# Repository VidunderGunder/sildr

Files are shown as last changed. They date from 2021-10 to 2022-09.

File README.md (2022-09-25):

# Sildr

Everything Sildr and technical.

1.0 and 2.0 are legacy, and some relevant documentation can be found in `/legacy`. Keep in mind it's mostly in Norwegian.

## Order History

**Components:**  
https://no.mouser.com/OrderHistory/OrdersView.aspx  
Email: kristiankramas@outlook.com  
Username: `vidundergunder`  
Password: `******`

**PCB:**  
https://jlcpcb.com/order#EL  
Email: kristiankramas@outlook.com  
Username: `vidundergunder`  
Password: `******`

## Electrical System v3.0

### Overview Illustration (click on image to open Figma):

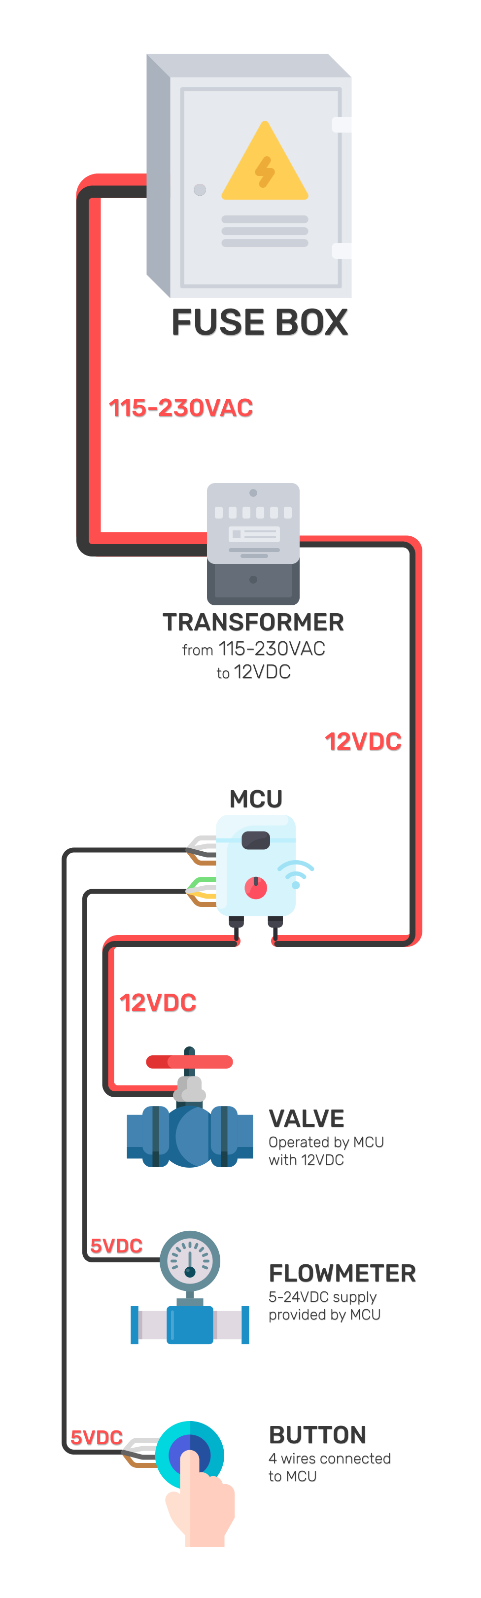
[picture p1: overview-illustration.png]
overview-illustration (https://www.figma.com/file/0GwcSEPVadjQJGAlymwUbZ/Sildr-Electronics?node-id=0%3A1)


The system is split in two parts:

1. Base system
2. Optional data logging system (requires the base system)

### Base System

#### Simplified circuit diagram (click on image to run simulation):

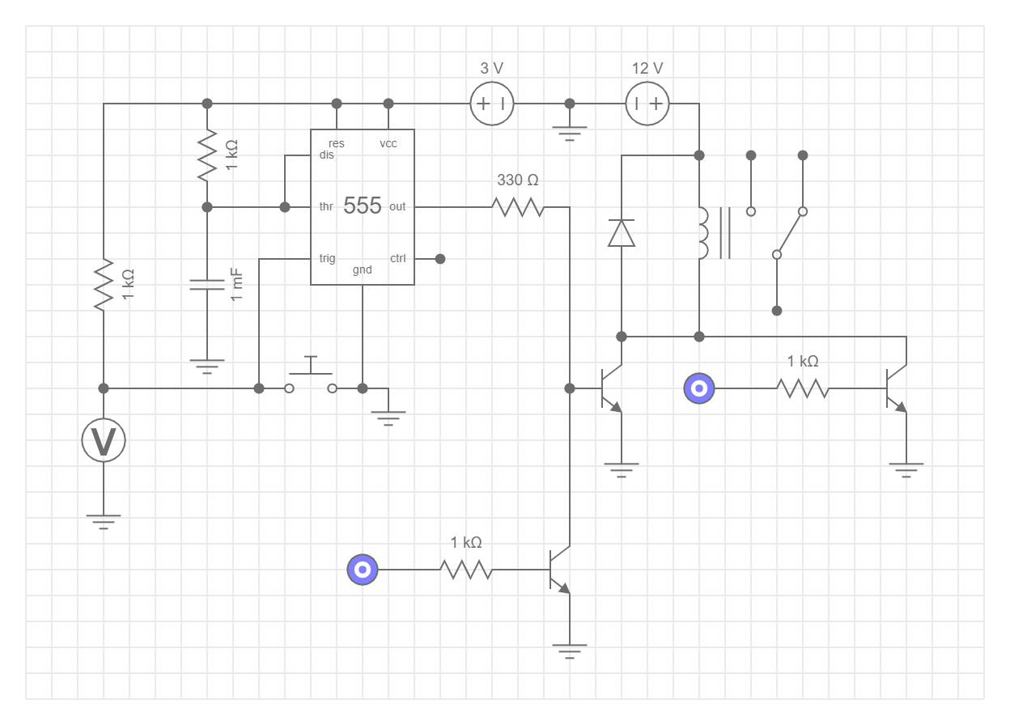
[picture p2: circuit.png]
circuit (https://everycircuit.com/circuit/6050376572469248/sildr-v3.0-base)


> _Image may be outdated_
> 
> - Behavior can be controlled with an MCU, and has an analog fallback
> - Relay represents the solenoid valve
> - Voltmeter is a digital in pin, registering 0V as button presses
> - Logic sources are digital out pins
> - Resistor connected to pin 7 and 6 on the 555-timer can be changed out for a potentiometer to manually set timer on-site

#### Simulated Prototype Circuit (click on image to run simulation):

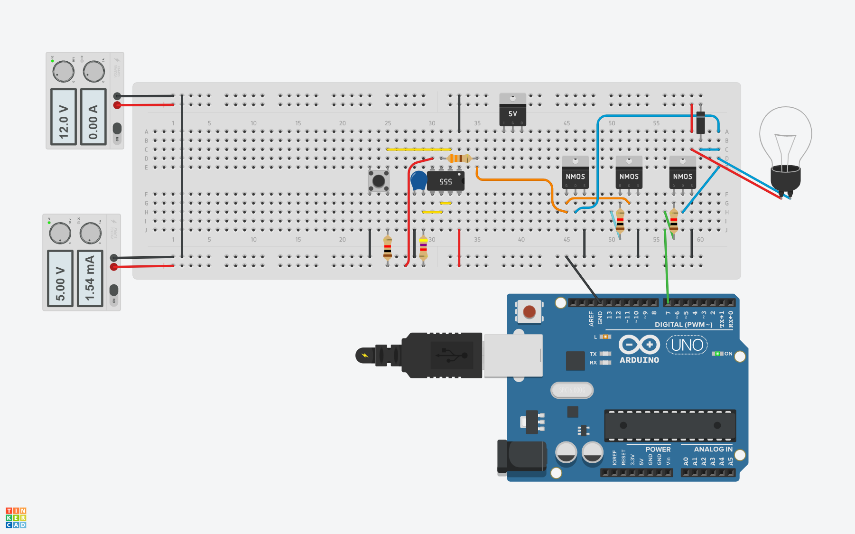
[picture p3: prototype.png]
prototype (https://www.tinkercad.com/things/aFhGxdh2pm7-epic-kieran-snaget/editel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)


> _Image may be outdated_  
> 
> - Simulation requires an Autodesk account (you can use your google account)
> - Lightbulb represents the solenoid valve

#### Prototype Components

- 1x 555-timer
- 3x nMOS Transistor (MOSFET)  
(FQP30N06L 60V LOGIC N-Channel MOSFET)
- 3x 1k resistor
- 1x 4k7 resistor
- 1x 330 resistor
- 1x 1mF capacitor
- 1x Pushbutton
- 1x diode
- 12V DC power supply
- 5V DC power supply

#### Production Components

| Component | Description | Image |
| --- | --- | --- |
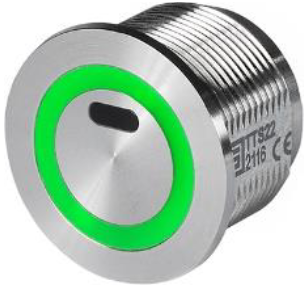
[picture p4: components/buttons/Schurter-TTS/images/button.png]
| Button | [Schurter Touchless Switch TTS](https://www.schurter.com/en/datasheet/TTS) |  |
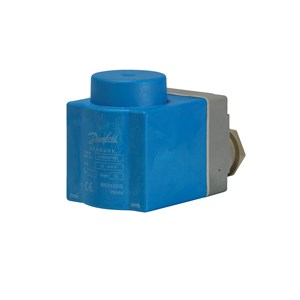
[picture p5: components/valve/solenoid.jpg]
| Solenoid Coil (Valve) | [Danfoss BE012DS Coil](https://store.danfoss.com/no/no/Climate-Solutions-for-cooling/Ventiler/Ventilspoler/Spoler-for-Magnetventiler/Magnetventilspole%2C-BE012DS%2C-Koblingsboks%2C-Multipa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) |  |
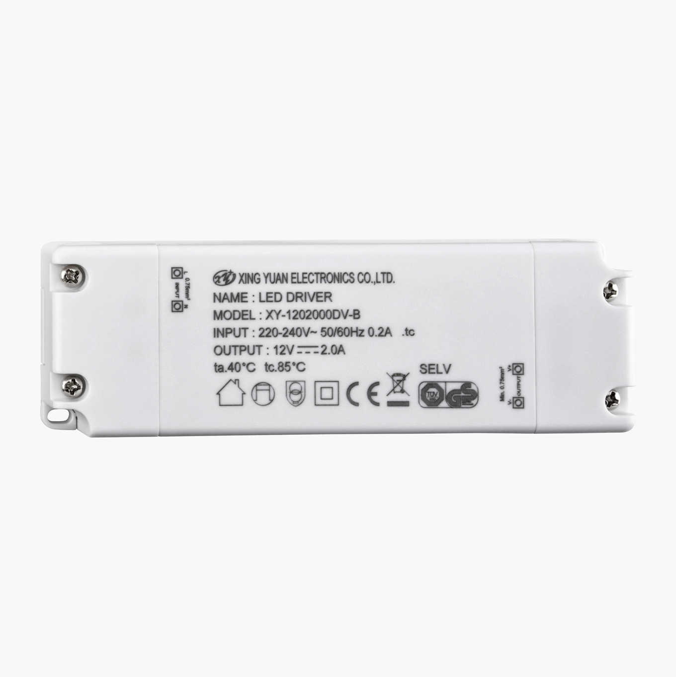
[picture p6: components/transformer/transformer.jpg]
| Transformer | [230VAC to 12VDC 2.0A (NB: Pick correct option)](https://www.biltema.no/en-no/construction/electrical-installations/lamp-sockets/led-transformer-12-v-dc-2000038013) |  |

### Data Logging System (optional)

_TODO_

| Component | Description | Image |
| --- | --- | --- |
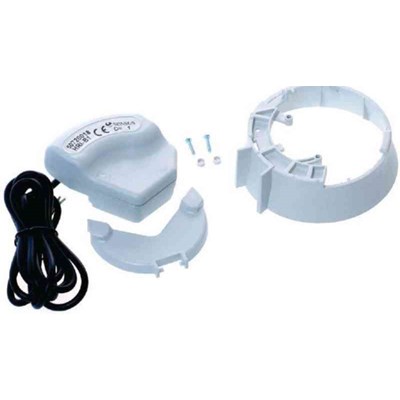
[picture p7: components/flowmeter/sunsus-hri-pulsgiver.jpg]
| Flowmeter | [Sensus HRI Pulsgiver](https://www.ahlsell.no/products/vvs-teknisk-produkter/ventiler---filter-og-instrumenter/vannmalere-med-tilbehor/4021402/) (1pulse/liter) [Datasheet](https://nobb-vavvs.no/API/Produktfiler/LastNed?id=27486&inline=) |  |

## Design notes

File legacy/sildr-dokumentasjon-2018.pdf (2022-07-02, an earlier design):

SILDR | SYSTEMOVERSIKT | 25.09.2018

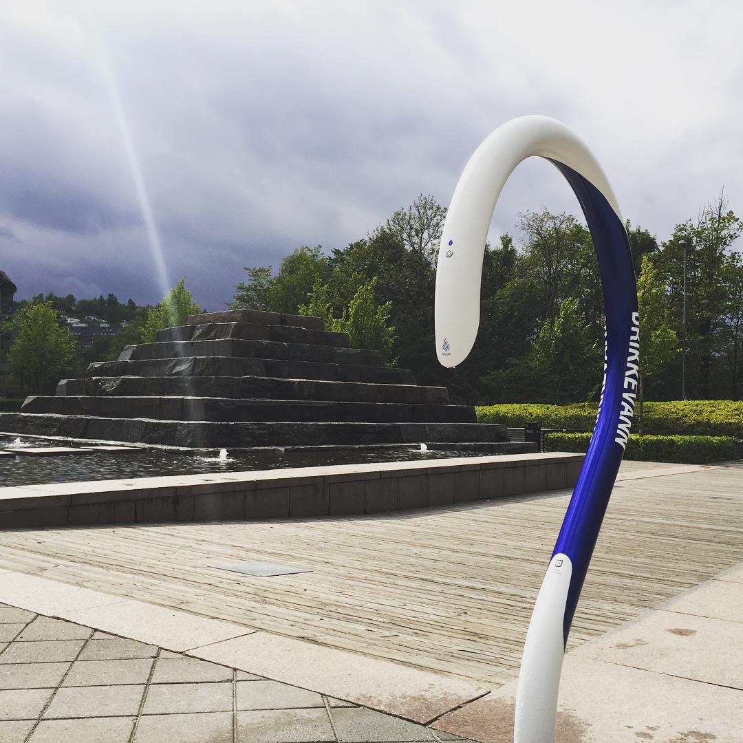
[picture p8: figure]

# Side 1 av 14

# FONTENE

# ELEKTRONIKK

Komponenter (Essensielle) | Kommentar | Illustrasjon

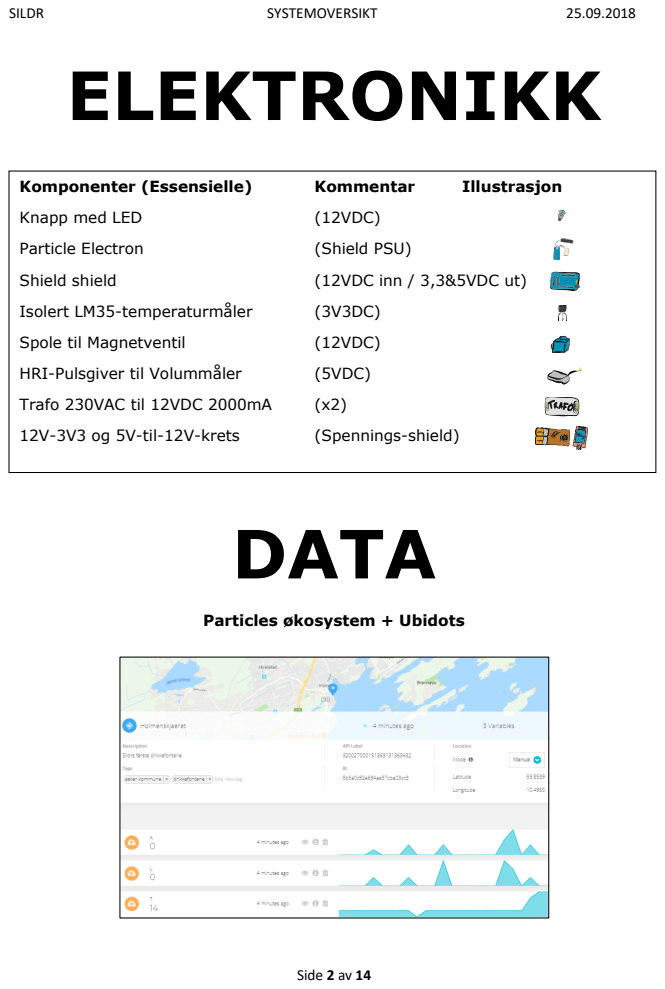
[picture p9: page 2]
Side 2 av 14; DATA; Knapp med LED; (12VDC); Particle Electron; (Shield PSU); Shield shield; (12VDC inn / 3,3&5VDC ut); Isolert LM35-temperaturmåler; Spole til Magnetventil; HRI-Pulsgiver til Volummåler; (5VDC); Trafo 230VAC til 12VDC 2000mA; 12V-3V3 og 5V-til-12V-krets; (Spennings-shield)

Particles økosystem + Ubidots

# RØRSYSTEMET

# Temperaturmåler

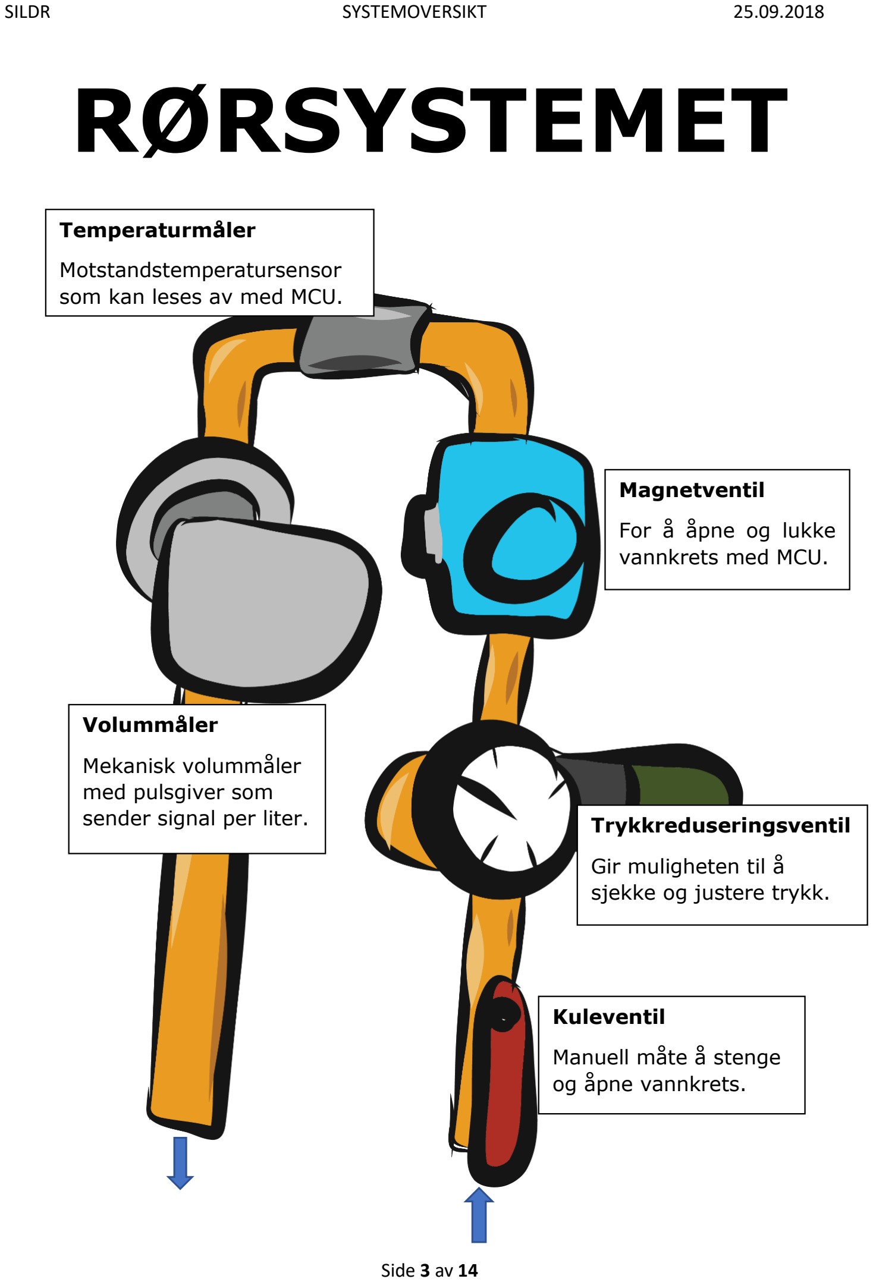
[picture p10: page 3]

# Side 3 av 14

# Magnetventil

# For å åpne og lukke

vannkrets med MCU.

# Trykkreduseringsventil

# Gir muligheten til å

sjekke og justere trykk.

# Volummåler

# Mekanisk volummåler med pulsgiver som

sender signal per liter.

# Motstandstemperatursensor

som kan leses av med MCU.

# Kuleventil

# Manuell måte å stenge

og åpne vannkrets.

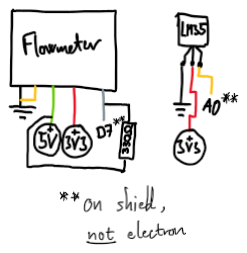
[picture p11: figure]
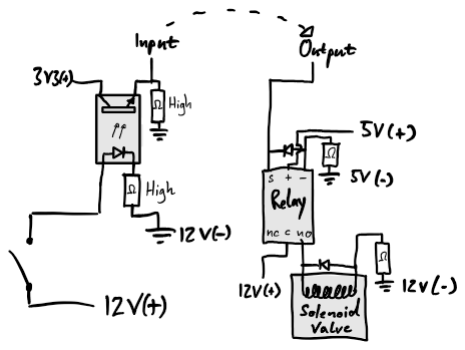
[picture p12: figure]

# Side 4 av 14

# KRETS

# ELDRE UTSTYRSLISTE

# Detaljert utstyrsliste for tidligere montering av elektronikk (med linker):

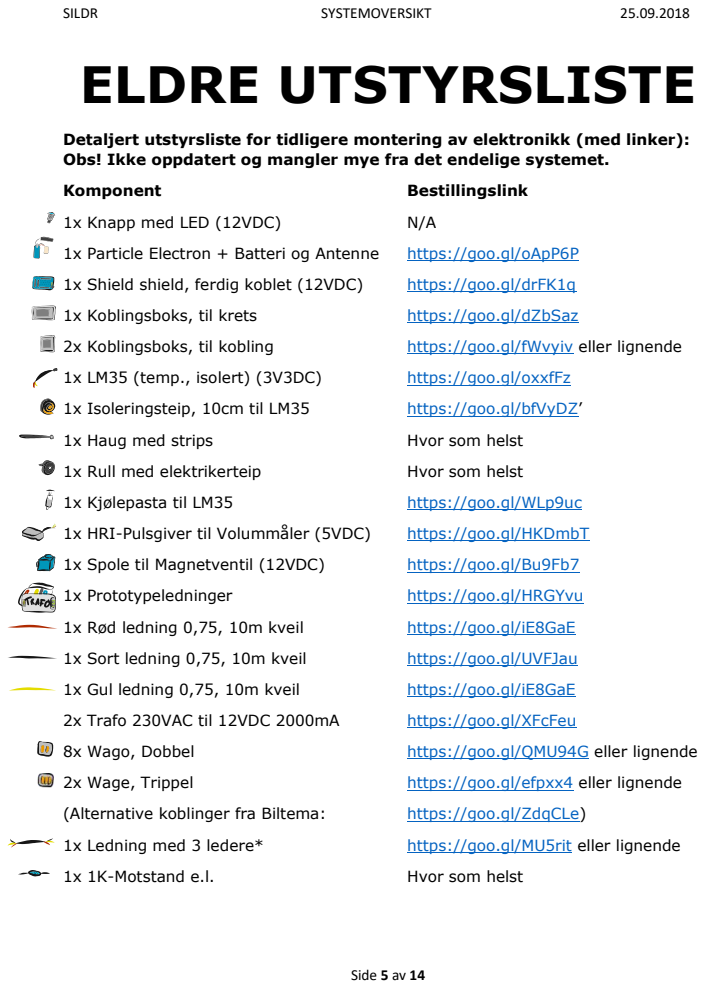
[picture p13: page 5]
Side 5 av 14; Komponent; Bestillingslink; 1x Knapp med LED (12VDC); 1x Particle Electron + Batteri og Antenne; https://goo.gl/oApP6P; 1x Shield shield, ferdig koblet (12VDC); https://goo.gl/drFK1q; 1x Koblingsboks, til krets; https://goo.gl/dZbSaz; 2x Koblingsboks, til kobling; https://goo.gl/fWvyiv eller lignende; 1x LM35 (temp., isolert) (3V3DC); https://goo.gl/oxxfFz; 1x Isoleringsteip, 10cm til LM35; https://goo.gl/bfVyDZ’; 1x Haug med strips; Hvor som helst; 1x Rull med elektrikerteip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

Obs! Ikke oppdatert og mangler mye fra det endelige systemet.

# ELDRE TEGNING AV SYSTEM

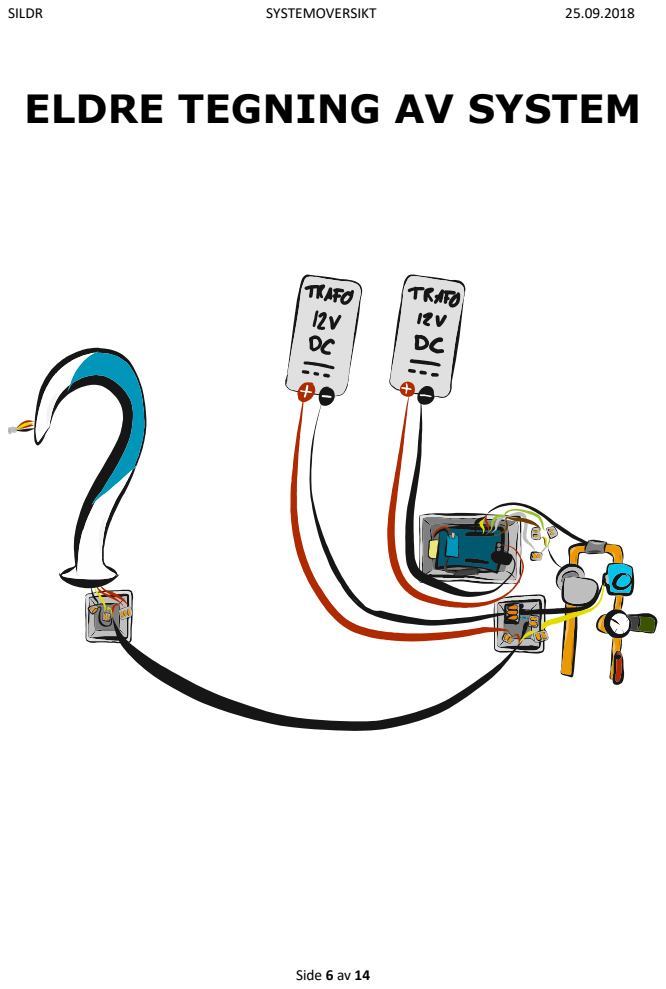
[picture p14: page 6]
Side 6 av 14

# Side 7 av 14

# PROBLEMER

- Fukt - Knapp - Har foreløpig blitt løst ved å gradvis øke debounce - Temperatursensor - Har opplevd mistenkelig høye temperaturer en ca. måned etter installasjon - Skal byttes til vannsikker pt100 (om jeg husker rett) - Monterings- og sammensetningstid - System og montering bør strømlinjeformes - Kretsen skal designes til ett kretskort med intuitiv I/O - Krets og rørsystem skal integreres til ett - Skal være ferdig koblet før montering - Overgang mellom spenninger - Bruker foreløpig hjemmesnekret overgang mellom spenninger - Ønsker å utbedre løsning dersom det finnes åpenbart bedre

løsninger.

# - Strømforbruk - Ingen oversikt over effekt - Må forbedres hvis overgang til batteri eller vannkraft som strømtilførsel - Knotete kode - Skyldes at vi er ferske - Skal skrives på nytt med leselighet og redigerbarhet i fokus

# Side 8 av 14

# PLANER/IDÉER

- Gjøre system robust - Gjøre system enkelt å reparere for en gjennomsnittlig elektriker/rørlegger - Intuitiv fjernstyring av fontener (justere enkle parametere og skru av og på) - Automatiske feilmeldinger - Automatiske software-fixes (f.eks. ved åpenbar støy i knapp og temperatur) - Vann som strømtilførsel

- Touchknapp (med hardware fra f.eks. Microchip, men krever mye utvikling), se siste del av dokument.

# - Automatisert analyse og fremstilling av data - API for kunder som ønsker å behandle tall selv

# Side 9 av 14

# KODE

//,,/'`\,,/'`\,,/'`\,,/'`\,,/'`\,,/'`\,,/'`\,,/'`\,,/'`\,,/'`\,,/'`\,,/'`\,,/'`\,,/'`\,,/'`\,,/'`\,,/'`\,// /*
(#/,
,/(/ ..
.(#, .*#(
.*#( | (#(,
,((,./#(. | ,. | *, | (( | .//.
.(#, /#/. | /(/. | | | ,. | (( | .,,,,.. | .//. | ..
*#(..(#. | ,#(. | *(#((((((((((((((/, .(* | (( | /(#(/'''/(#(/,,//. | .,((((((##/*.
/*#/ ,#( | ,((* | ** | *(* | .(* | (( | /(/, | ,/(##/. | .*#(,. | ,/#/
(#/.,((* | /#*..*#(. | .//, | .(* | (( | .*#/ | .(#/. .(#. | ,((,
.*#( | /#*. ,##. *((* | ,#(. | .(* | (( | ,(*. | *(/..*(* | .#(
.(#*. ,#(. ,(#/ .(#*.., | .*(##########((/. | .(* | (( | *(, | ,//..//. | ,,
.(#(* | ,((* | /#(, ,#( | */ | /**. .(* | (( | ,(/. | *(*..//.
/*, | ,/#(. | .##, ./(* | (#. | ((* .(* | (( | ,#( | ,#(. .//.
.,(#(* | ./#(. *(/, .##. | .#(, .(* | (( | /#*, | .*((, | .//.
.((#(*. | .(#*. .(#, ./#/' | .,,,,,,,,,,,,,,/(/, | .(* | (( | ./#(/','/(((* | .//.
.. | /*#(* | ./#/ | *(/, | .,/////////////*,. | *, | ,, | ''(/((,. | .,,.
.,/(##/* | .(#*. ,(/
.*,. | .,(#(* | //.
,'/(*/
//,,/'`\,,/'`\,,/'`\,,/'`\,,/'`\,,/'`\,,/'`\,,/'`\,,/'`\,,/'`\,,/'`\,,/'`\,,/'`\,,/'`\,,/'`\,,/'`\,,/'`\,//

//LIBRARIES
#include <Ubidots.h>

Ubidots ubidots("BBFF-HNmFokn0E81qqRQwXxBjI05L2pF1tD");

//SYSTEM
SYSTEM_MODE(SEMI_AUTOMATIC);
SYSTEM_THREAD(ENABLED);

//PINS
const byte button_pin | = A1;
const byte valve_pin | = D6;
const byte flow_pin | = D7;
const byte temperature_pin | = A0;

//VARIABLES
//Valve
bool new_activate = true;
bool new_activate_count = true;
bool valve_first_if_statement_done = false; int activate_count = 0;
unsigned long activate_time_interval = 7000; unsigned long activate_time_initial = millis(); unsigned long activate_time;
unsigned long before_current = millis(); unsigned long before_initial = millis(); unsigned long valve_debounce_before = 200;

//Flow
bool new_flow = true;
bool new_pulse = true;
unsigned long new_flow_current; unsigned long new_flow_initial; unsigned long before_initial_flow; unsigned long before_current_flow; int flow_count = 0;

//Temperature
unsigned long temperature_time_initial = millis(); unsigned long temperature_interval = 5000;
int temperature_counts = 0;
int celsius_average;
float temperature_reading;
float celsius_sum = 0;
int temperature_calibration = -6;

//Publish
bool new_publish = true;
unsigned long publish_interval = 10*60*1000; unsigned long publish_window = 10000;

# Side 10 av 14

//,,/'`\,,/'`\,,/'`\,,/'`\,,/'`\,,/'`\,,/'`\,,/'`\,,/'`\,,/'`\,,/'`\,,/'`\,,/'`\,,/'`\,,/'`\,,/'`\,,/'`\,//

/*_____
/ ____| | _
| (___ | ___| |_ _ | _ _ __
\___ \ / _ \ __| | | | '_ \
____) | __/ |_| |_| | |_) |
|_____/ \___|\__|\__,_| .__/
| | | | |*/

void setup() {

pinMode(button_pin, INPUT); pinMode(valve_pin, OUTPUT); pinMode(flow_pin, INPUT);
pinMode(temperature_pin, INPUT);

if (!Particle.connected()) { Particle.connect();
}

delay(1000);
}

/*_
| | | ___ | ___ | _ __
| | | / _ \ / _ \| '_ \
| |___| (_) | (_) | |_) |
|______\___/ \___/| .__/
| | | | |*/

void loop() {
valve();
publish();
flow();
temperatureAnalog();
}

//,,/'`\,,/'`\,,/'`\,,/'`\,,/'`\,,/'`\,,/'`\,,/'`\,,/'`\,,/'`\,,/'`\,,/'`\,,/'`\,,/'`\,,/'`\,,/'`\,,/'`\,//

/*_ | __ | _ | =()=
\ \ | / / | | | | ,/'\_||_
\ \ | / /_ _| |_ | _____ | ( (___ | `.
\ \/ / _` | \ \ / / _ \ | `\./ | `=='
\ | / (_| | |\ V / | __/ | |||
\/ \__,_|_| \_/ \___| | \*|||*/

void valve() {

int button_press = digitalRead(button_pin);

activate_time = millis() - activate_time_initial; if (button_press) {
if (new_activate) {
before_initial = millis();
new_activate = false;
| }
before_current = millis() - before_initial; if (before_current >= valve_debounce_before) { if (new_activate_count) {
activate_count += 1;
new_activate_count = false;
| }
digitalWrite(valve_pin, HIGH); activate_time_initial = millis(); before_initial = millis();
| }
valve_first_if_statement_done = true;
} else if (activate_time < activate_time_interval && !button_press && valve_first_if_statement_done) { digitalWrite(valve_pin, HIGH);
new_activate = true;
before_initial = millis();
} else {
digitalWrite(valve_pin, LOW); new_activate = true;
before_initial = millis(); valve_first_if_statement_done = false; new_activate_count = true;

# Side 11 av 14

}
}

void activatePublish() {
print("A", activate_count); activate_count = 0;
}

/*______ _
| | ____| | | // //
| |__ | | | _____ | __ | ||| |||
| | __| | |/ _ \ \ /\ / / | \\\ \\\
| | | | | (_) \ V | V / | ||| |||
|_| | |_|\___/ \_/\_/ | // | */

void flow() {

int flow = digitalRead(flow_pin);

if (!flow) {
if (new_pulse) {
before_initial_flow = millis(); new_pulse = false;
}

before_current_flow = millis() - before_initial_flow;

if (before_current_flow >= 70 && new_flow) { flow_count += 1;
new_flow = false;
new_flow_initial = millis();
}
} else {
new_flow_current = millis() - new_flow_initial;

if (new_flow_current >= 54) {
new_flow = true;
new_pulse = true;
}
}
}

void flowPublish() {
print("L", flow_count);
flow_count = 0;
}
/*_______ | ,*'*,
|__ | __| | _ | | --|
| | ___ _ __ ___ | _ __ | ___ _ __ __ _| |_ _ | _ _ __ ___ | | §-|
| |/ _ \ '_ ` _ \| '_ \ / _ \ '__/ _` | __| | | | '__/ _ \ | | §-|
| | | __/ | | | | | |_) | | __/ | | (_| | |_| |_| | | | | __/ ,* ,§, *,
|_|\___|_| |_| |_| .__/ \___|_| | \__,_|\__|\__,_|_| | \___| | | *@* | |
| | | *,___,*
|*/

void temperatureAnalog() {
if (millis() - temperature_time_initial >= temperature_interval) { temperature_reading = analogRead(temperature_pin);

float mv = (((temperature_reading + 1) / 4095.0) * 3300.0); float celsius = (mv / 10) + temperature_calibration;

temperature_time_initial = millis();
temperature_counts += 1;

celsius_sum += celsius;
celsius_average = celsius_sum / temperature_counts; }
}

void temperaturePublish() { print("T", celsius_average); temperature_counts = 0;
celsius_sum = 0;
}

# Side 12 av 14

/*_____ | _ | _ _ | _
| | __ \ | | | | | (_) | | | | ,*,
| |__) | | _| |__ | |_ ___| |__ | ,* | *,
| | ___/ | | | '_ \| | / __| '_ \ | | | |
| | | | |_| | |_) | | \__ \ | | | | | | |
|_| | \__,_|_.__/|_|_|___/_| |_| | |__*/

void publish() {
if (new_publish && millis() % publish_interval <= publish_window && millis() > publish_window) { if (!Particle.connected()) {
Particle.connect();
}
activatePublish();
flowPublish();
temperaturePublish();
ubidots.sendAll();
new_publish = false;
} else if (millis() % publish_interval > publish_window) new_publish = true;
}

//,,/'`\,,/'`\,,/'`\,,/'`\,,/'`\,,/'`\,,/'`\,,/'`\,,/'`\,,/'`\,,/'`\,,/'`\,,/'`\,,/'`\,,/'`\,,/'`\,,/'`\,//

/*_____ | _ | ______
| | __ \ | (_) | _ | | | \
| |__) | __ _ _ __ | | | | </> | |
| | ___/ '__| | '_ \| __| | | ----- |
| | | | | | | | | | | |__ | | ----- |
|_| | |_| | |_|_| |_|\__/ | |______*/

void print(char* name, int value) { ubidots.add(name, value);
}

# Extra: TOUCHKNAPP

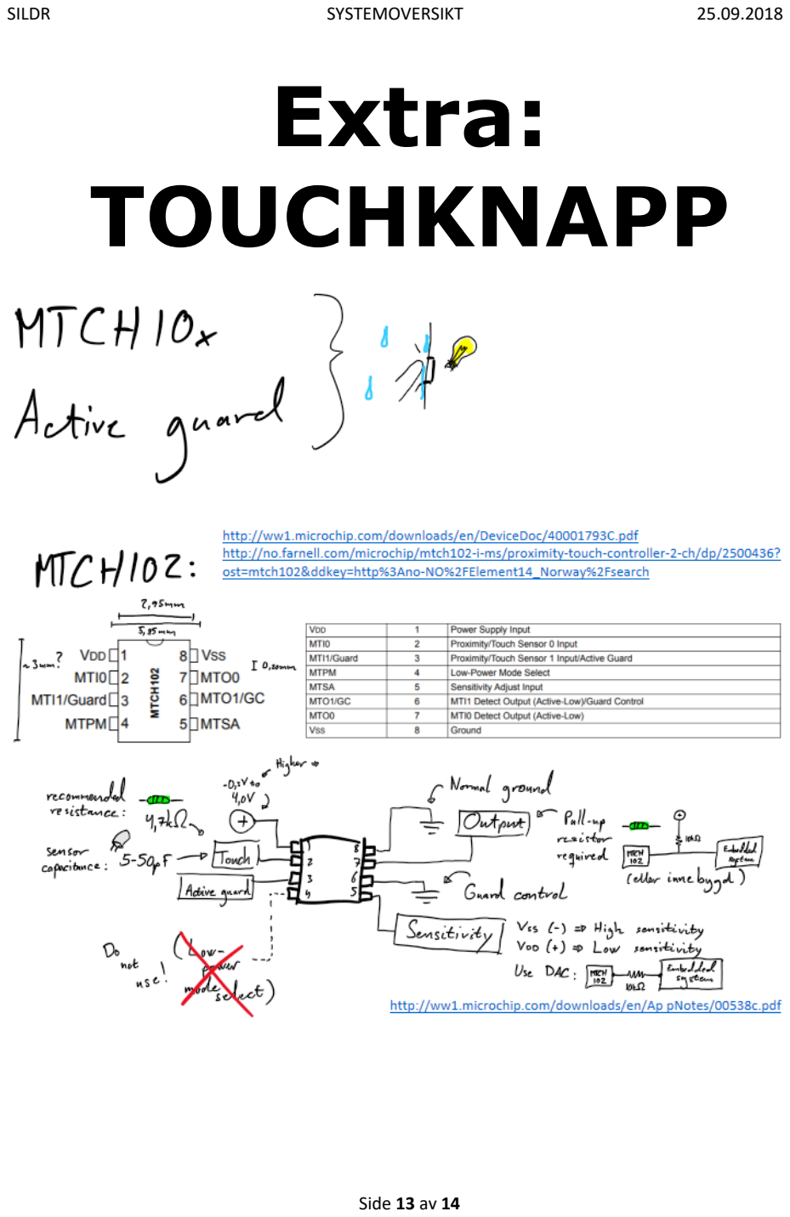
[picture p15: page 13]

# Side 13 av 14

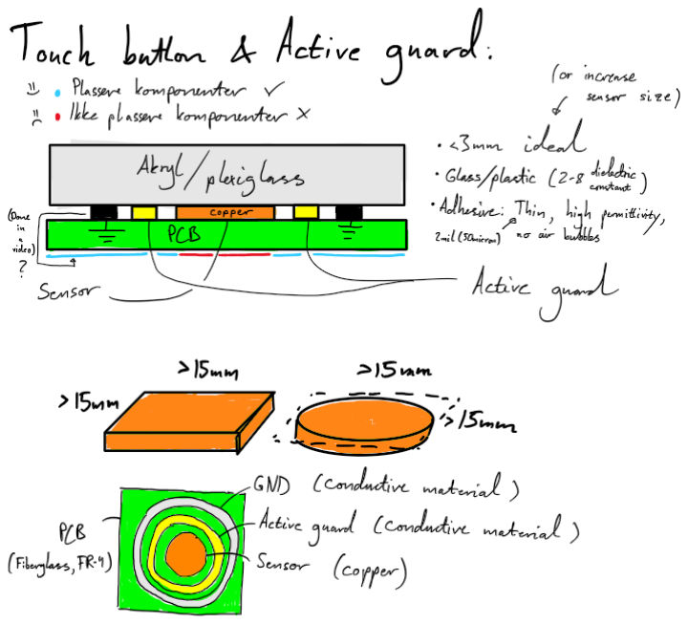
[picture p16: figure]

# Side 14 av 14

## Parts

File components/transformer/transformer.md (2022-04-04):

# Transformer

https://www.biltema.no/en-no/construction/electrical-installations/lamp-sockets/led-transformer-12-v-dc-2000038013

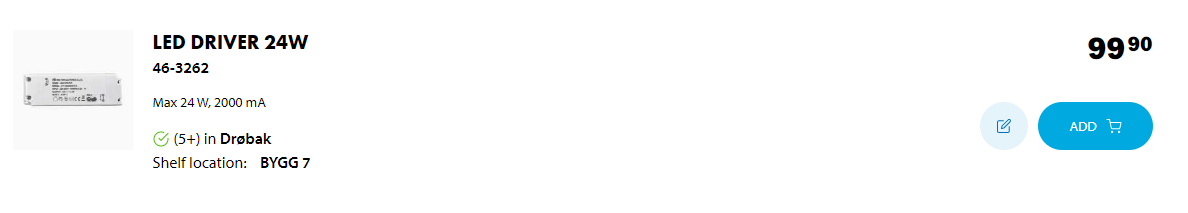
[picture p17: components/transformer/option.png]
Option to choose


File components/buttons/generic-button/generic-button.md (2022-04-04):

# Generic Switch

https://www.aliexpress.com/item/32907768532.html?spm=a2g0s.9042311.0.0.27424c4dfxDNNu

Expected delivery time: 1-4 weeks (check shipping options)

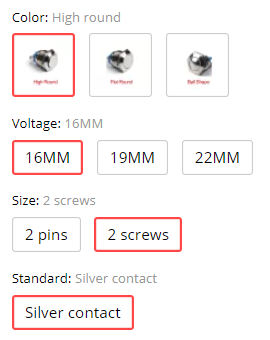
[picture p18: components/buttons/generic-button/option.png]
Option to choose


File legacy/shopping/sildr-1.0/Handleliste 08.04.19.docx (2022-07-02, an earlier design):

SILDR - HANDLELISTE

Arrow:

https://www.arrow.com/

PRODUKTNR. BESKRIVELSE ANTALL

- PC817X3NSZ1B Opto 6
- 314010016 Temp 6
- 1N4004 Diode 6
- COM-08375 Kondensator 12
- VAOL-5MSBY2 LED 12
- CCF601K00FKE36 1K Ohm 12
- CCF6010K0FKE36 10K Ohm 24
- 2N5191G Transistor 6
- 2940 Header 6
- BRN402 MCU 4

Kommentar:

Listen skal inneholde 10 ulike ting.

Alle antall i listen er doblet, med unntak av MCU (som bare har én ekstra), siden de koster litt. WiFi-variant til testing finnes på Eik allerede.

Mouser:

https://no.mouser.com/

PRODUKTNR. BESKRIVELSE ANTALL

- 710-691412320010 Terminal 4
- 710-691412320004’ Terminal 4
- 485-3931 Boks 4
- 474-PRT-11375 Ledninger 1

Kommentar:

Listen skal inneholde 4 ulike ting.

Terminal og Boks har én ekstra, i tilfelle defekter eller uhell. Dette er komponenter som ikke lett blir ødelagt, så flere reservedeler trengs ikke.

JLCPCB:

https://jlcpcb.com/

1. Velg «Quote Now»
2. Dra og slipp zip-fila «Gerber Files» på nettleseren
  a. Alternativt trykk på «Add your gerber file» og velg filen.
  b. Det funket hvis du ser bildet av kretskortet på skjermen.
3. Endre disse verdiene til føgnede:
  a. PCB Qty: 10
  b. Surface Finish: Lead Free HASL-RoHS
4. Trykk på “SAVE TO CART”
5. Fullfør bestilling.

Annet:

PRODUKTNR. BESKRIVELSE ANTALL

- ??? Magnetventil 1

Kommentar:

Listen skal inneholde 1 ting.

Vi hadde samme flowmeter, men ikke magnetventil. Bruker i mellomtiden en tilsvarende magnetventil i litt mindre størrelse.

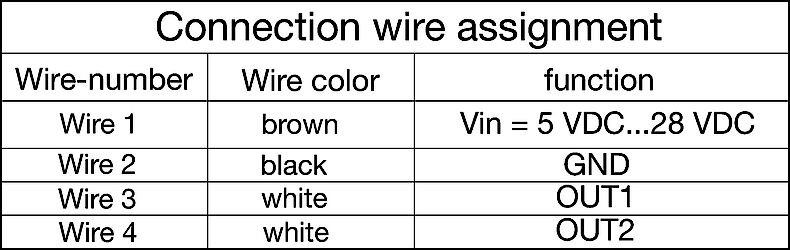
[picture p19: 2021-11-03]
components/buttons/Schurter-TTS/images/wires.jpg

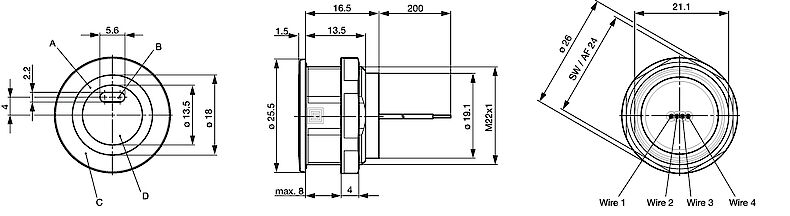
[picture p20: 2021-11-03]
components/buttons/Schurter-TTS/images/dimensions.jpg

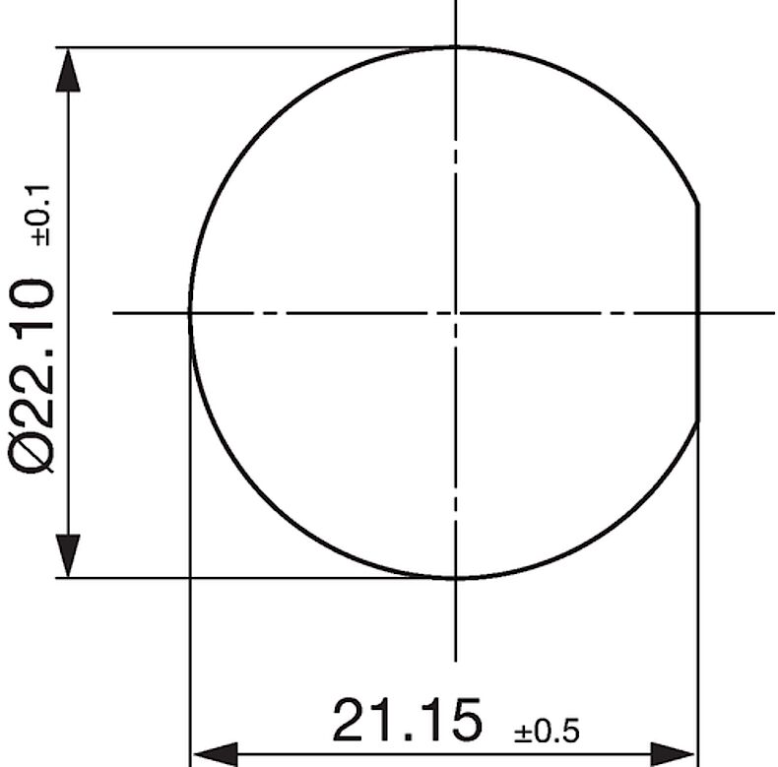
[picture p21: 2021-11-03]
components/buttons/Schurter-TTS/images/mounting-hole.jpg

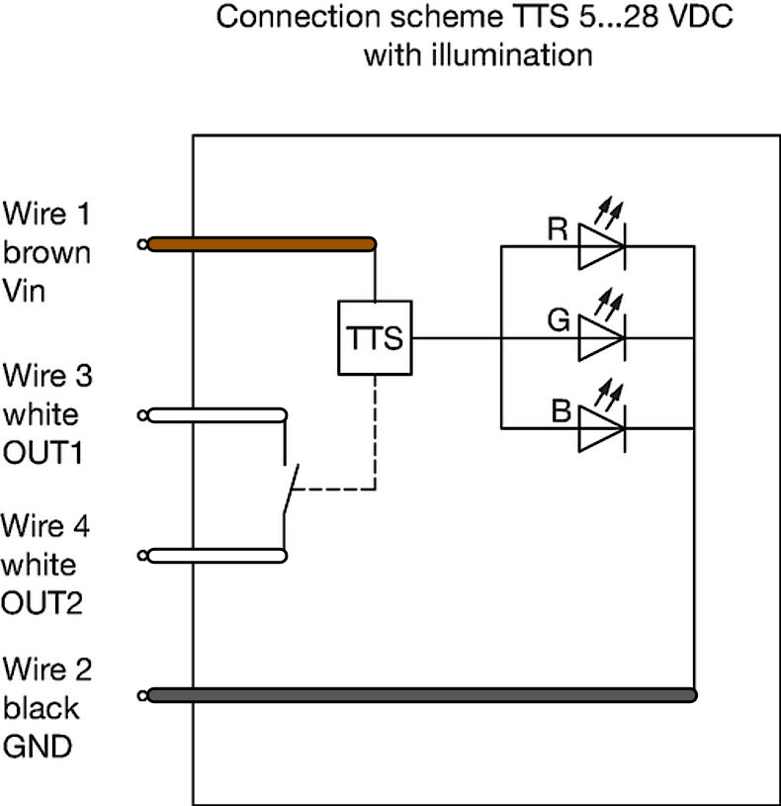
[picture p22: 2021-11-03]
components/buttons/Schurter-TTS/images/button-circuit.png

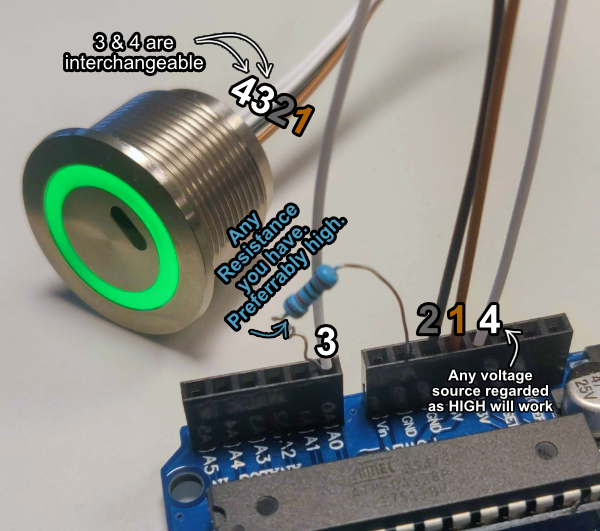
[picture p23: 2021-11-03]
components/buttons/Schurter-TTS/images/arduino-circuit.png

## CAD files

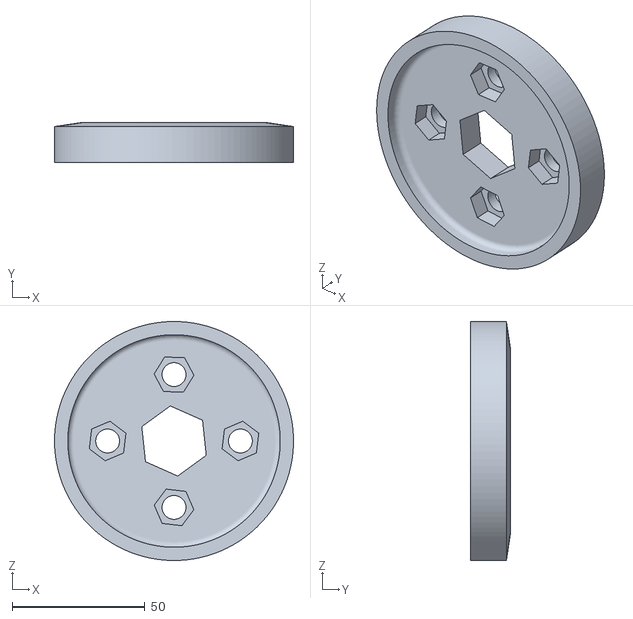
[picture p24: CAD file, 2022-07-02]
components/3D-print/Fat.stl
90.0 x 15.0 x 90.0

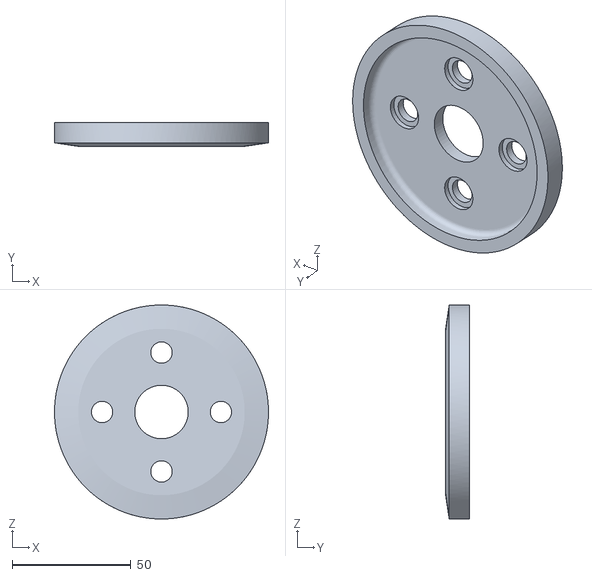
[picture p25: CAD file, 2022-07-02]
components/3D-print/Slim.stl
90.0 x 10.0 x 90.0

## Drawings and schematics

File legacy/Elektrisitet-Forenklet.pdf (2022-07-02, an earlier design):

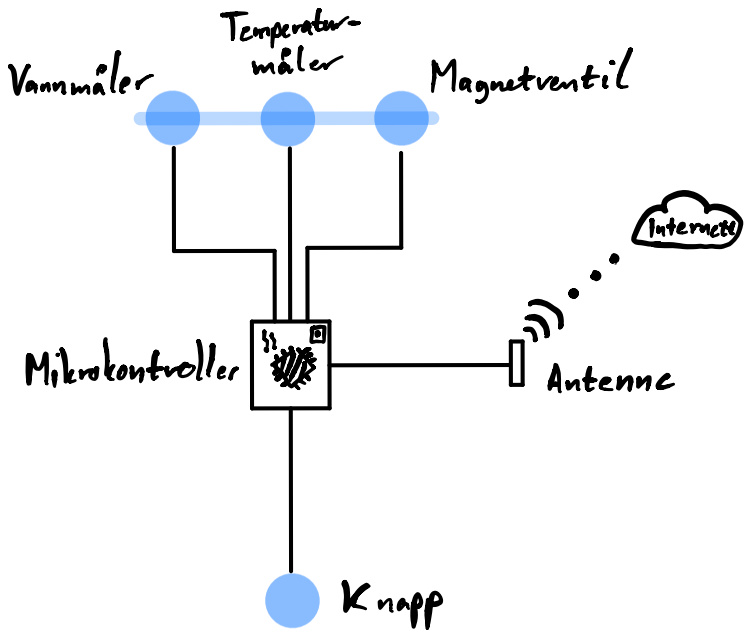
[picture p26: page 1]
Temperature; Vannmaeler; matter; Magnetrentil; Mihrokontroller; Antenne; Knapp

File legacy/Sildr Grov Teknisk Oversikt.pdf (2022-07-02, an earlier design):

## Vannknets

# Forenklet

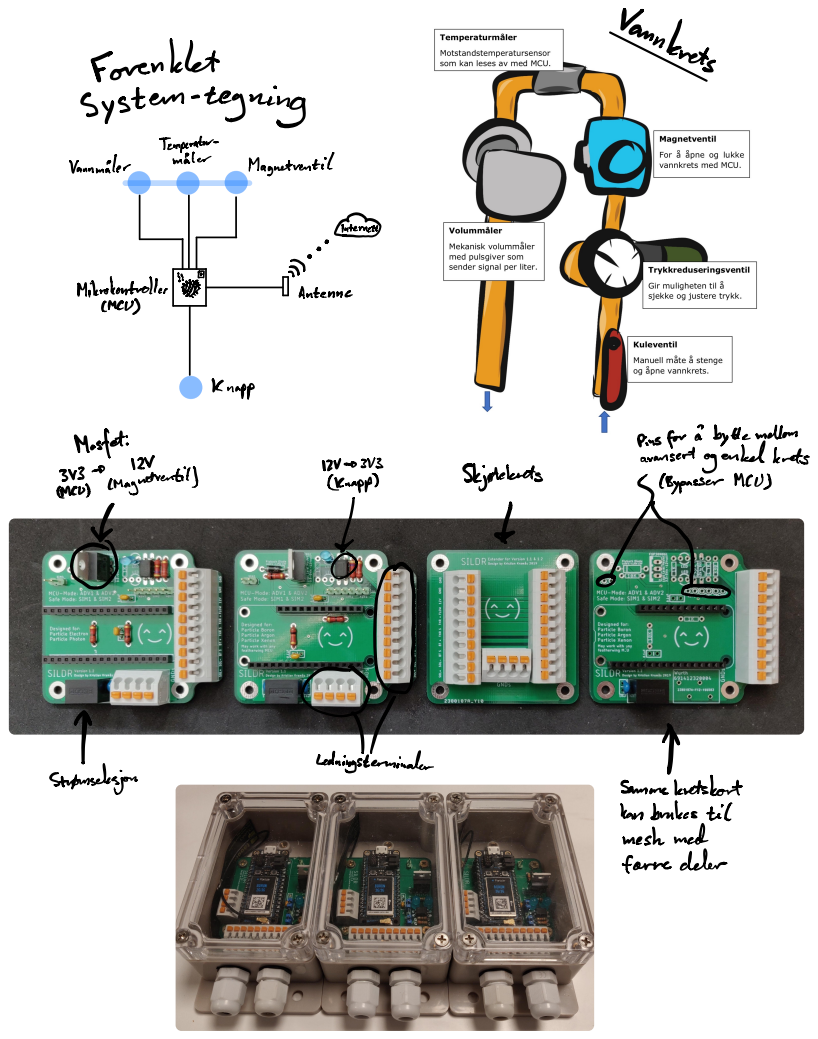
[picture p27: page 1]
system teguing; Temperature; Vannmaeler; Water; Magnetrentil; Interned; Mihrokontroller; P Antenne; MCU; Knapp; Mosfet; pinsfordbyttemellom; aransertogenkeltenets; µco; imagnetrentil; app; Skjolteknets; gCBypasser MCO; Strolusselesjon; Ledningsterminaler; p Sammekutskort; hanbmkestic meshmed farredeler

## Batter

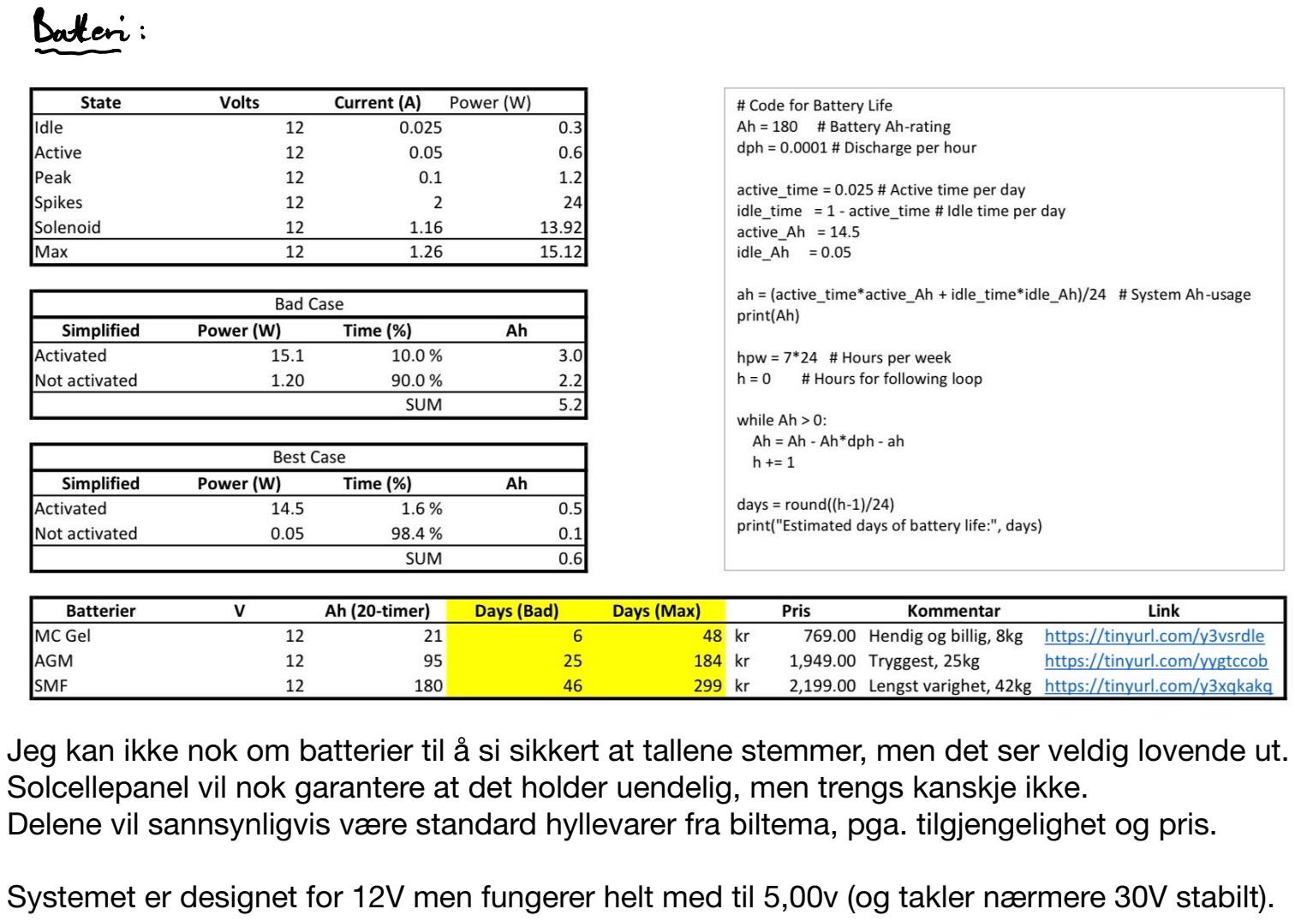
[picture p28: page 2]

Jeg kan ikke nok om batterier til å si sikkert at tallene stemmer, men det ser veldig lovende ut. Solcellepanel vil nok garantere at det holder uendelig, men trengs kanskje ikke.
Delene vil sannsynligvis være standard hyllevarer fra biltema, pga. tilgjengelighet og pris.

Systemet er designet for 12V men fungerer helt med til 5,00v (og takler nærmere 30V stabilt).

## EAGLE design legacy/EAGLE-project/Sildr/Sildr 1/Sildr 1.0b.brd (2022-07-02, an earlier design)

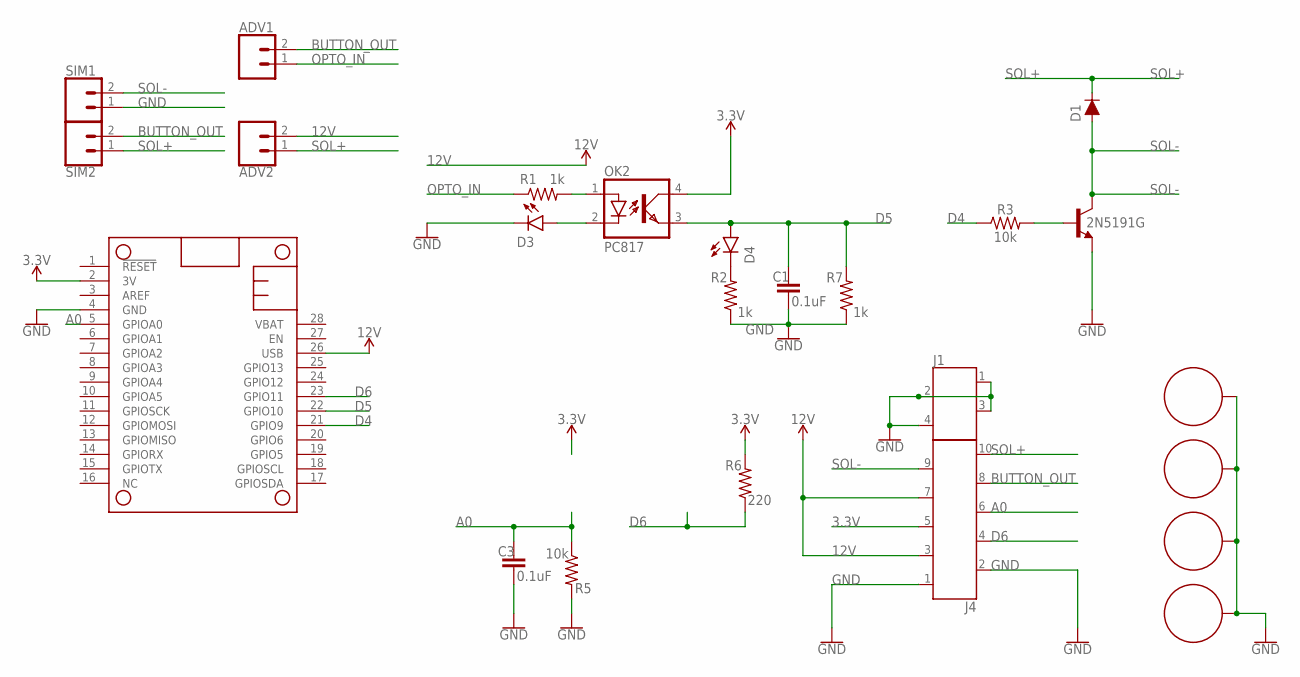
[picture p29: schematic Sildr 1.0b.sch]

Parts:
2N5191G: 2SC1944; T-30_V
ADV1, ADV2: CONN_02; 1X02
C1, C3: 0.1uF; CAP-PTH-SMALL-KIT
D1: 1A/50V/1.1V; DIODE-1N4001
D3, D4: LED3MM; LED_3MM
H1, H2, H3, H6: STANDOFF_ELECTRICAL; STANDOFF-ELECTRICAL
J1: 691412320004
J4: 691412320010
MS1: FEATHERWING_NODIM; FEATHERWING_DIM
OK2: PC817; DIL04
R1, R2, R7: 1k; AXIAL-0.3
R3, R5: 10k; AXIAL-0.3
R6: 220; AXIAL-0.3
SIM1, SIM2: CONN_02; 1X02

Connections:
3.3V: J4.5, MS1.2 (3V), OK2.4 (COL), R6.P$2 (2)
12V: ADV2.2, J4.3, J4.7, MS1.26 (USB)
A0: C3.1, J4.6, MS1.5 (GPIOA0), R5.P$1 (1)
BUTTON_OUT: ADV1.2, J4.8, SIM2.2
D4: MS1.21 (GPIO9), R3.P$1 (1)
D5: C1.1, D4.A, MS1.22 (GPIO10), OK2.3 (EMIT), R7.P$2 (2)
D6: J4.4, MS1.23 (GPIO11), R6.P$1 (1)
GND: 2N5191G.3 (E), C1.2, C3.2, D3.K (C), H1.P1, H2.P1, H3.P1, H6.P1, J1.1, J1.2, J1.3, J1.4, J4.1, J4.2, MS1.4 (GND), R2.P$1 (1), R5.P$2 (2), R7.P$1 (1), SIM1.1
unnamed: 2N5191G.1 (B), R3.P$2 (2)
unnamed: D3.A, OK2.2 (C)
unnamed: OK2.1 (A), R1.P$2 (2)
unnamed: D4.K (C), R2.P$2 (2)
OPTO_IN: ADV1.1, R1.P$1 (1)
SOL+: ADV2.1, D1.C, J4.10, SIM2.1
SOL-: 2N5191G.2 (C), D1.A, J4.9, SIM1.2

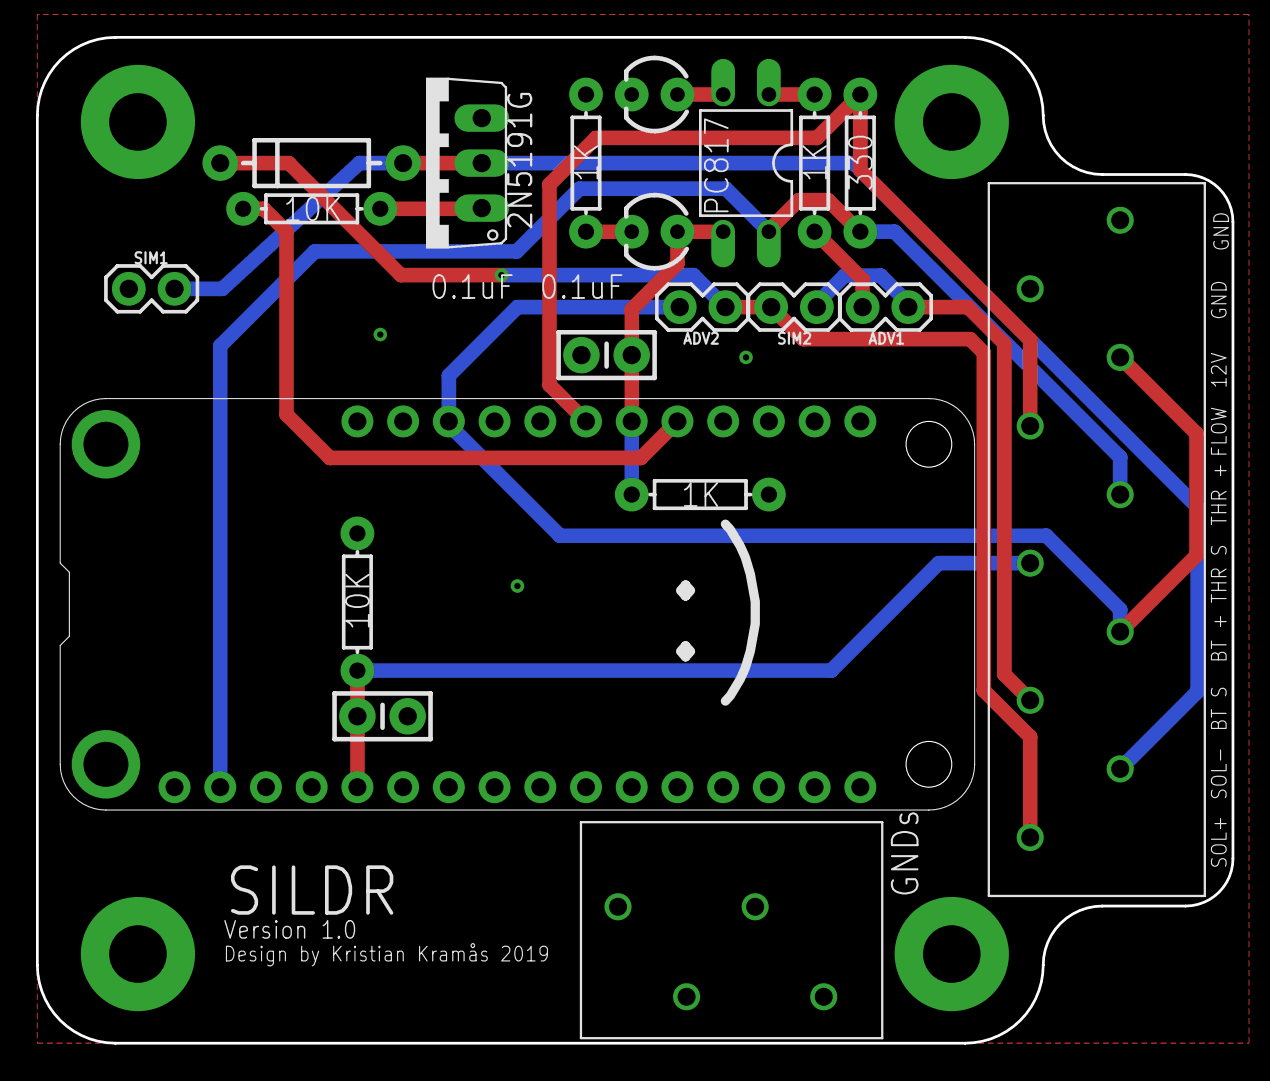
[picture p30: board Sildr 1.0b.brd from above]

Board: 2 copper layers, 66.4 x 55.9 mm, 24 parts (0 on the bottom side), 15 nets.

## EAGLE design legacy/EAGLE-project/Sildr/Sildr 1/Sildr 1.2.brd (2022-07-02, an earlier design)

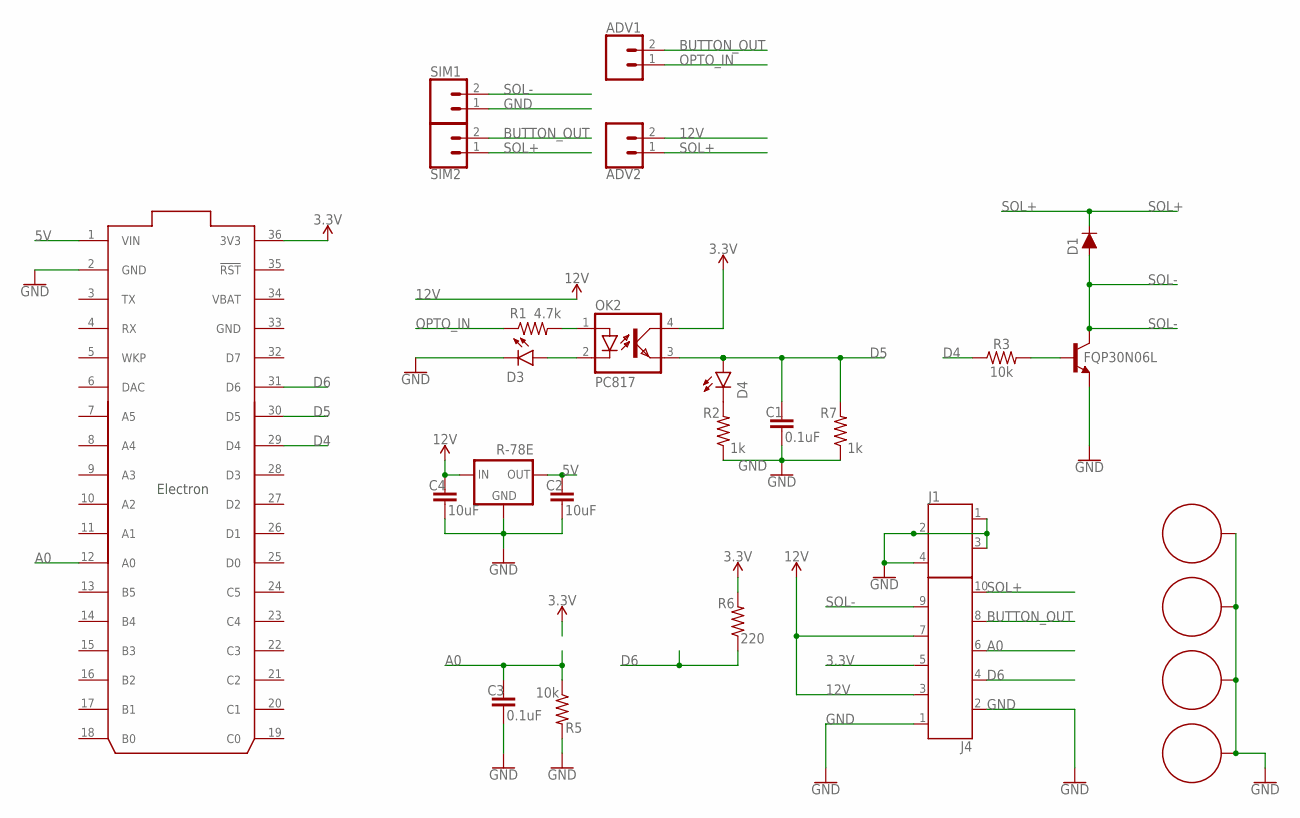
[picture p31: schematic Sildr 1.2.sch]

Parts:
ADV1, ADV2: CONN_02; 1X02
C1, C3: 0.1uF; CAP-PTH-SMALL-KIT
C2, C4: 10uF; CAP-PTH-SMALL-KIT
D1: 1A/50V/1.1V; DIODE-1N4001
D3, D4: LED3MM; LED_3MM
FQP30N06L: 2SC1944; T-30_V
H1, H2, H3, H6: STANDOFF_ELECTRICAL; STANDOFF-ELECTRICAL
J1: 691412320004
J4: 691412320010
OK2: PC817; DIL04
R1: 4.7k; AXIAL-0.3
R2, R7: 1k; AXIAL-0.3
R3, R5: 10k; AXIAL-0.3
R6: 220; AXIAL-0.3
R-78E: R-78E5.0-1.0; DC-DC_CONVERTER_78XX
SIM1, SIM2: CONN_02; 1X02
U$1: ELECTRON_WITH_HEADERS; ELECTRON

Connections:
3.3V: J4.5, OK2.4 (COL), R6.P$2 (2), U$1.36 (3V3)
5V: C2.1, R-78E.VOUT (OUT), U$1.1 (VIN)
12V: ADV2.2, C4.1, J4.3, J4.7, R-78E.VIN (IN)
A0: C3.1, J4.6, R5.P$1 (1), U$1.12 (A0)
BUTTON_OUT: ADV1.2, J4.8, SIM2.2
D4: R3.P$1 (1), U$1.29 (D4)
D5: C1.1, D4.A, OK2.3 (EMIT), R7.P$2 (2), U$1.30 (D5)
D6: J4.4, R6.P$1 (1), U$1.31 (D6)
GND: C1.2, C2.2, C3.2, C4.2, D3.K (C), FQP30N06L.3 (E), H1.P1, H2.P1, H3.P1, H6.P1, J1.1, J1.2, J1.3, J1.4, J4.1, J4.2, R2.P$1 (1), R5.P$2 (2), R7.P$1 (1), R-78E.GND, SIM1.1, U$1.2 (GND), U$1.33 (GND)
unnamed: FQP30N06L.1 (B), R3.P$2 (2)
unnamed: D3.A, OK2.2 (C)
unnamed: OK2.1 (A), R1.P$2 (2)
unnamed: D4.K (C), R2.P$2 (2)
OPTO_IN: ADV1.1, R1.P$1 (1)
SOL+: ADV2.1, D1.C, J4.10, SIM2.1
SOL-: D1.A, FQP30N06L.2 (C), J4.9, SIM1.2
VBAT: U$1.34 (VBAT)

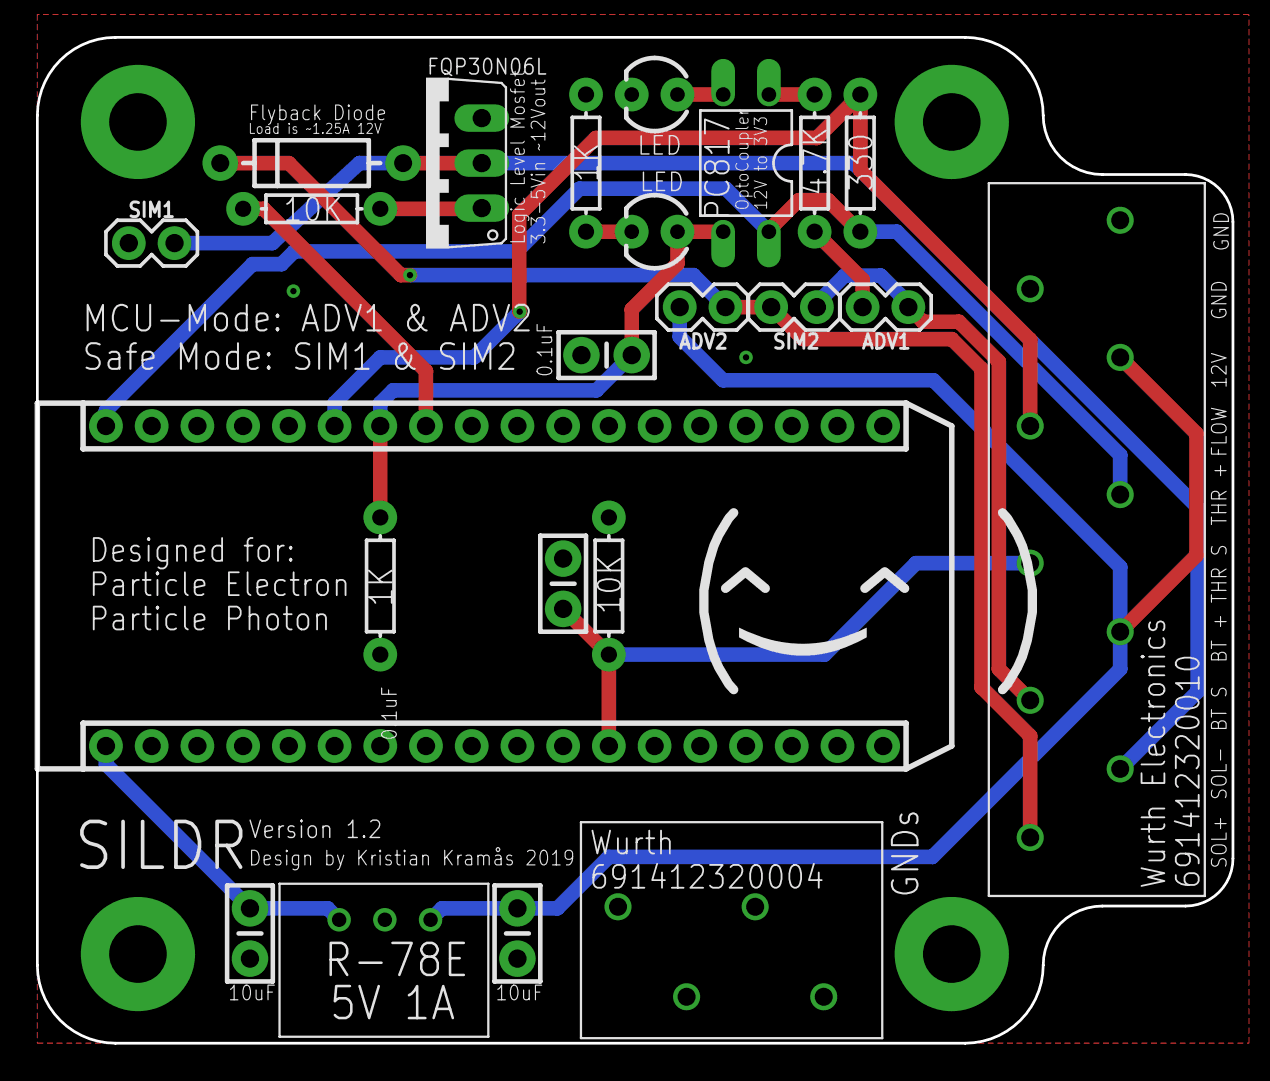
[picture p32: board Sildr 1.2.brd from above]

Board: 2 copper layers, 66.4 x 55.9 mm, 27 parts (0 on the bottom side), 16 nets.

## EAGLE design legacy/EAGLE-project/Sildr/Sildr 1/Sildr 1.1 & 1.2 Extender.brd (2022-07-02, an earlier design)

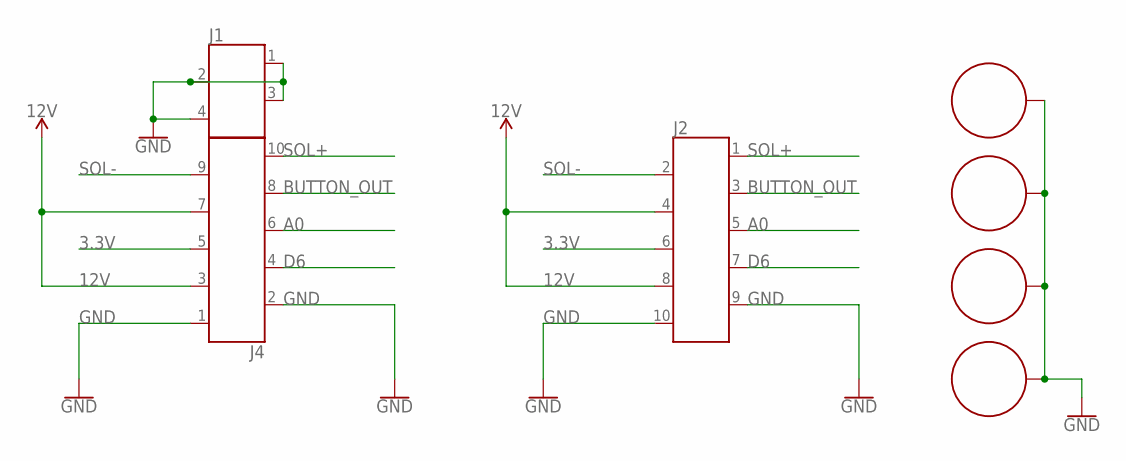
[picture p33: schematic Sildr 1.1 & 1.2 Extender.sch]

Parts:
H1, H2, H3, H6: STANDOFF_ELECTRICAL; STANDOFF-ELECTRICAL
J1: 691412320004
J2, J4: 691412320010

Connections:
3.3V: J2.6, J4.5
12V: J2.4, J2.8, J4.3, J4.7
A0: J2.5, J4.6
BUTTON_OUT: J2.3, J4.8
D6: J2.7, J4.4
GND: H1.P1, H2.P1, H3.P1, H6.P1, J1.1, J1.2, J1.3, J1.4, J2.9, J2.10, J4.1, J4.2
SOL+: J2.1, J4.10
SOL-: J2.2, J4.9

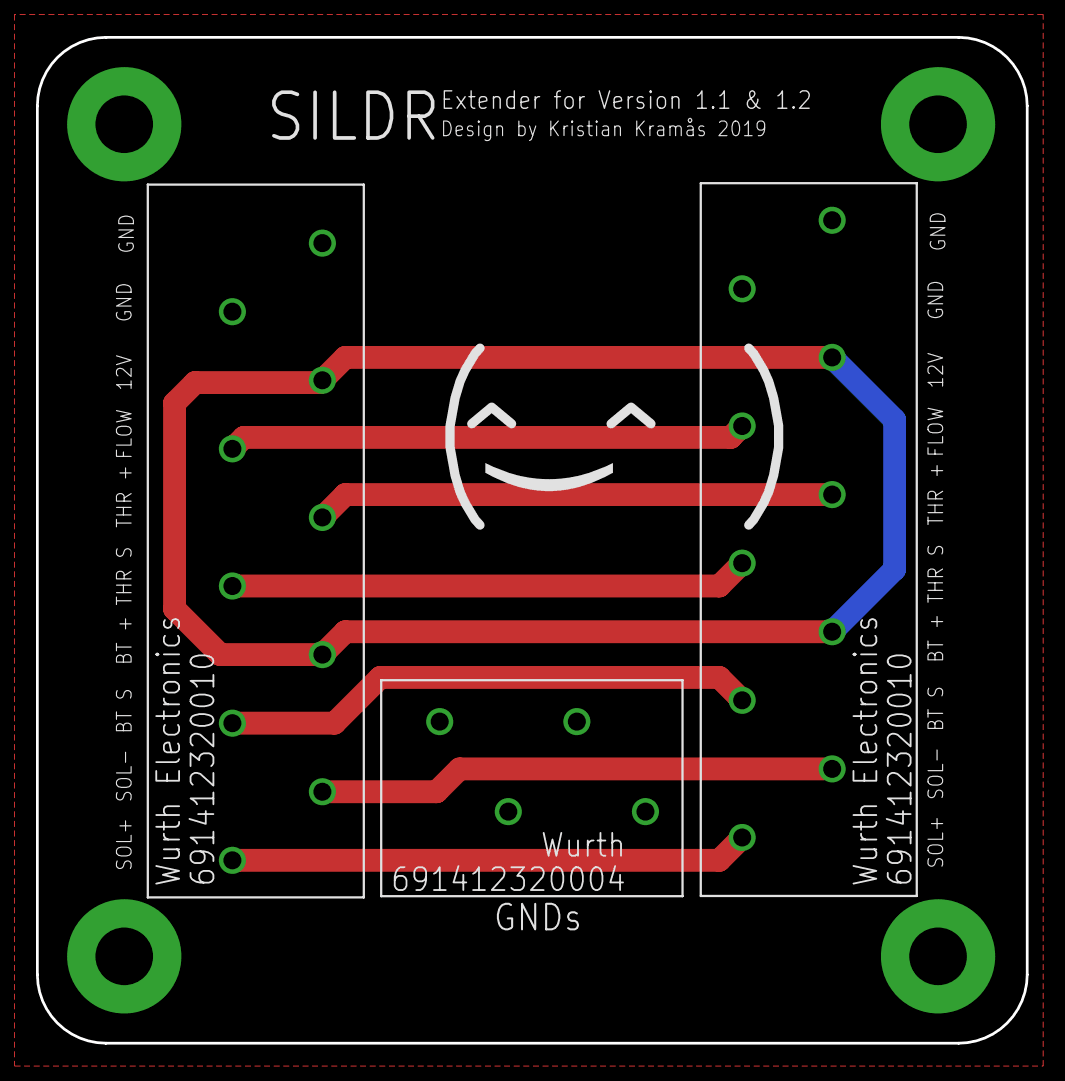
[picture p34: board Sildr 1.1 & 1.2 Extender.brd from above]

Board: 2 copper layers, 55.0 x 55.9 mm, 7 parts (0 on the bottom side), 8 nets.

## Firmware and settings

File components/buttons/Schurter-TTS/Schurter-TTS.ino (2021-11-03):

const int buttonPin = A0;

float readAnalogPin(int outPin)
{
    return (analogRead(A0) / 1023.0) * 5.0;
}

int logPin(int pin)
{
    float voltage = readAnalogPin(pin);
    Serial.println("A0: " + String(voltage) + "V");
}

void setup()
{
    Serial.begin(115200);
    pinMode(buttonPin, INPUT);
}

void loop()
{
    logPin(buttonPin);
    delay(100);
}

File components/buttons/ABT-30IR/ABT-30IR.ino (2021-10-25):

const int ledPin = 13;

void setup()
{
    Serial.begin(115200);
    pinMode(ledPin, OUTPUT);
    pinMode(A0, INPUT);
}

void loop()
{
    digitalWrite(ledPin, LOW);
    const float inputVoltage = (analogRead(A0) / 1023.0) * 5.0;
    if (inputVoltage >= 5.0)
    {
        Serial.println("DANGER: MAX VOLTAGE REACHED - ARDUINO MIGHT GO BOOM.");
    }
    if (inputVoltage > 0.25)
    {
        digitalWrite(ledPin, HIGH);
    }
    else
    {
        digitalWrite(ledPin, LOW);
    }
    Serial.println(String(inputVoltage) + "V");
    Serial.flush();
    delay(100);
}

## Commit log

2021-11-03 Added Schurter TTS buttons
2022-07-02 Legacy docs and new circuit
    [Fat.stl, SILDR Batteri v1.x.xlsx, Sildr 1.0b.brd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]
2022-07-02 Updated circuit
2022-07-03 4k7 to 1k resistor to simplify BOM
2022-07-03 Circuit Details
2022-07-03 Prototype Circuit ++
2022-07-03 Prototype image during sim

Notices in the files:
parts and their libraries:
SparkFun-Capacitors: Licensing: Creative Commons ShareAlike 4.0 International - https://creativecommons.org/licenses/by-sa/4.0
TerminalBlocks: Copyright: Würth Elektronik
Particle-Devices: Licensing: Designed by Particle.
